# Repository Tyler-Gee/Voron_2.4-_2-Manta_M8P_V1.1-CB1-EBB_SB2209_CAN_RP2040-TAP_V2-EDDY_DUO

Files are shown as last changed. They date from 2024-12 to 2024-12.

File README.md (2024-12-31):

---
created: 2024-12-19T14:11
updated: 2024-12-22T21:22
---
# TODO
1. Create pdf Manual Chapters files for ever step. These files will follow relative path so they can be opened from within the REAMME.md file

# Formbot Voron 2.4 V2.4 R2 Pro+ Kit
- Store Link: https://www.aliexpress.com/item/1005003385349518.html?spm=a2g0o.order_list.order_list_main.59.318318027IHoca
- Github: Github: https://github.com/FORMBOT/Voron-2.4
- Review and Guide: https://www.youtube.com/watch?v=7x-eafpESLc

















# Components
## VoronDesigns:
github: https://github.com/VoronDesign/Voron-2

## TAP V2
Github:  https://github.com/VoronDesign/Voron-Tap

## Stealthburner
Github: https://github.com/VoronDesign/Voron-Stealthburner

## EBB SB2209 CAN (RP2040)
Github: https://github.com/bigtreetech/EBB

## MANTA M8P V1.0 & V1.1:
Github:  https://github.com/bigtreetech/Manta-M8P

## CB1
Github: https://github.com/bigtreetech/CB1

## Eddy Duo
- Store Link: https://www.aliexpress.com/item/1005006344907714.html?spm=a2g0o.order_list.order_list_main.23.318318027IHoca
- Github: https://github.com/bigtreetech/Eddy







## Belter
Store Link: https://www.aliexpress.com/item/1005007144698835.html?spm=a2g0o.order_list.order_list_main.17.318318027IHoca
Github: https://github.com/bigtreetech/Belter-belt-tension-Tool/tree/master

# Build Guide
## Part 0.0: Introduction
Manual: VORON2 2.4R2 Build Guide
- Pages: 0 - 11

## Part 1.0: Frame
Manual: VORON2 2.4R2 Build Guide
- Pages: 12 - 21

## Part 2.0: Z Drives
Manual: VORON2 2.4R2 Build Guide
- Pages: 22 - 51

## Part 3.0: Print Bed
Manual: VORON2 2.4R2 Build Guide
- Pages: 52 - 61

## Part 4.0: A/B Drives And Idlers
Manual: VORON2 2.4R2 Build Guide
- Pages: 62 - 81

## Part 5.0: Gantry
Manual: VORON2 2.4R2 Build Guide
- Pages: 82 - 107

## Part 6.0: Z Axis
Manual: VORON2 2.4R2 Build Guide
- Pages: 108 - 123

## Part 7.0: A/B Belts
Manual: VORON2 2.4R2 Build Guide
- Pages: 124 - 128
- Pages: 132 - 138

## Part 8.0: Tool head - Stealthburner
### Part 8.1: ClockWork2 Extruder
Manual: VORON STEALTHBURNER
- Pages: 0 - 40

### Part 8.2: Tool Cartridge
Manual: VORON STEALTHBURNER
- Pages: 41 - 43

### Part 8.3: Stealthburner
Manual: VORON STEALTHBURNER
- Pages: 44 - 57

### Part 8.4: Tap V2
Manual: VORON TAP

### Part 8.5: EBB SB2209 CAN (RP2040)
Manual: SB2240\2209 CAN V1.0
- Pages: 0 - 24

## Part 9.0: Check A/B Belt Run Inspection
Manual: VORON2 2.4R2 Build Guide
- Page: 142
Manual: Belter User Manual

## Part 10.0: Electronics
Manual: VORON2 2.4R2 Build Guide
- Pages: 148 - 173

## Part 11.0: Wiring
Manual: VORON2 2.4R2 Build Guide
- Pages: 0 - 11
Manual: Wiring Instructions for Voron 2.4 Pro
- Pages: 0 - 11
Manual: Instruction of V2.4 R2 Pro+
Manual: BIGTREETECH MANTA M8P V1.0&V1.1 User Manual
- Page: 11
Manual: EBB SB2209 CAN V1.0（RP2040）Build Guide_20240219
- Page: 7

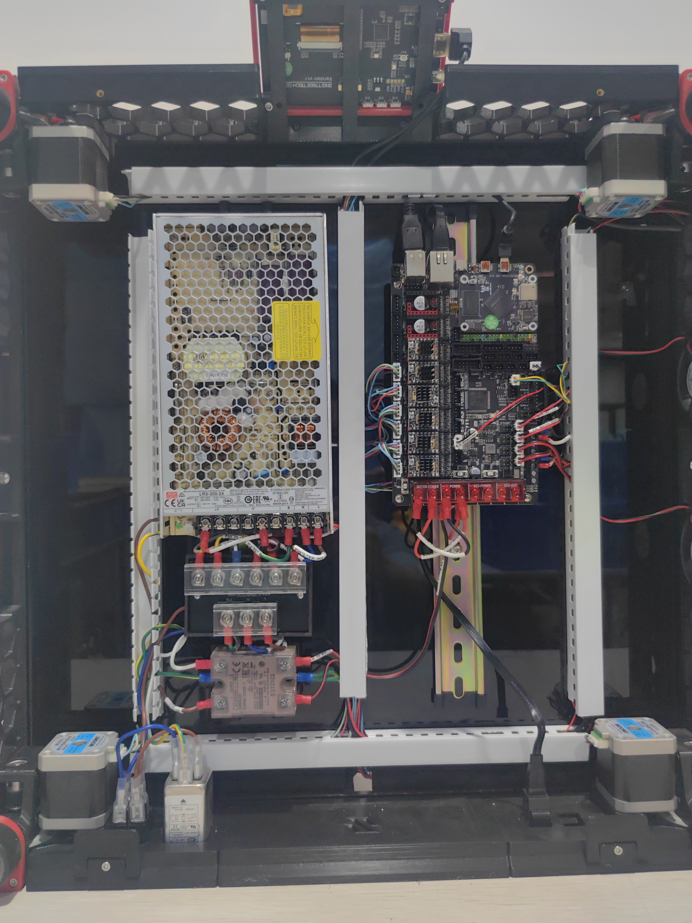
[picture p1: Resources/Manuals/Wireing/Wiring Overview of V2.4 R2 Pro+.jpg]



## Part 12.0: Manta M8P V1.1 + CB1
Manual: BIGTREETECH MANTA M8P V1.0&V1.1 User Manual
- Pages: 0 - 23

## Part 13.0: Skirts
Manual: VORON2 2.4R2 Build Guide
- Pages: 212 - 239

## Part 14.0: Panels
Manual: VORON2 2.4R2 Build Guide
- Pages: 240 - 259

## Part 16: Eddy Duo
Manual: BIGTRRETECH Eddy Series User Manual 20241210

# Flashing
## Overview
1. Put device into DFU Mode
2. Flash Katapult onto device
	- All devices of the same architecture flash the same way
	- Example: rp2040, stm, ect 
1. Put device into Katapult Mode
	- All devices of the same architecture flash the same way
	- Example: rp2040, stm, ect 
3. Flash klipper to device
4. Get UUID of canbus node

## OS Install
Manual: BIGTREETECH CB1 User Manual
- Pages: 13 - 18
Image: https://github.com/bigtreetech/CB1/releases

## MANTA M8P
Manual: BIGTREETECH MANTA M8P V1.0&V1.1 User Manual
- Pages: 33 - 39
Guides: 
1. @ [MAIN GUIDE]https://canbus.esoterical.online/mainboard_flashing.html
2. @ [MAIN RESOURCE]https://canbus.esoterical.online/mainboard_flashing/common_hardware/BigTreeTech%20Manta%20M8P%20v1.1/README.html
3. https://3dpandme.com/2022/10/02/tutorial-btt-manta-m8p-cb1-klipper-guide/
4. https://mpx.wiki/Firmware-Flash/flash-m8p-v1-ebb
5. https://gist.github.com/fredrikasberg/c14f08eb8617bf8981f77dbc01b00602
Github: https://github.com/bigtreetech/Manta-M8P

### DFU Mode
- Hold Boot0, Press Reset, Wait 5s, Release Boot0
### Flash Katapult
```bash
cd ~/katapult
make menuconfig
#	Micro-controller Architecture (STMicroelectronics STM32)  --->
#    Processor model (STM32G0B1)  --->
#    Build Katapult deployment application (8KiB bootloader)  --->
#    Clock Reference (8 MHz crystal)  --->
#    Communication interface (USB (on PA11/PA12))  --->
#    Application start offset (8KiB offset)  --->
#    USB ids  --->
#()  GPIO pins to set on bootloader entry
#[*] Support bootloader entry on rapid double click of reset button
#[ ] Enable bootloader entry on button (or gpio) state
#[*] Enable Status LED
#(PA13)  Status LED GPIO Pin

make clean
make

lsusb
## ID of STMicroelectronics STM DEvice in DFU Mode
## ID 0483:df11
sudo dfu-util -R -a 0 -s 0x08000000:leave -D ~/katapult/out/katapult.bin -d 0483:df11
```

### ### Enter Katapult Mode
- & double press reset button, red light indicates Katapult mode

### Flash Klipper
```bash
cd ~/klipper
make menuconfig
#[*] Enable extra low-level configuration options
#    Micro-controller Architecture (STMicroelectronics STM32)  --->
#    Processor model (STM32G0B1)  --->
#    Bootloader offset (8KiB bootloader)  --->
#    Clock Reference (8 MHz crystal)  --->
#    Communication interface (USB to CAN bus bridge (USB on PA11/PA12))  --->
#    CAN bus interface (CAN bus (on PD12/PD13))  --->
#    USB ids  --->
#(1000000) CAN bus speed
#()  GPIO pins to set at micro-controller startup
make clean
make
 
sudo service klipper stop
ls /dev/serial/by-id/
## usb-katapult_stm32g0b1xx_460041000A504B4633373520-if00
python3 ~/katapult/scripts/flashtool.py -f ~/klipper/out/klipper.bin -d /dev/serial/by-id/usb-katapult_your_board_id

ip -s -d link show can0
## Show bitrate is set to 1000000?

~/klippy-env/bin/python ~/klipper/scripts/canbus_query.py can0
## Found canbus_uuid=702c161f28a9, Application: Klipper
sudo service klipper start
```

## EBB SB2209C CAN RP2040 
Manual: EBB SB2209 CAN V1.0（RP2040）Build Guide_20240219
- Guides:
	1. @ [MAIN GUIDE]https://canbus.esoterical.online/toolhead_flashing
	2. @ [MAIN RESOURCE]https://canbus.esoterical.online/toolhead_flashing/common_hardware/BigTreeTech%20SB2209%20(RP2040)/README.html
	4. https://www.drklipper.de/doku.php?id=klipper_faq%3Aflash_guide%3Arp2040%3Aebb_sb2209_can
	5. https://www.youtube.com/watch?v=AYnoJCH7JJc&t=257s&ab_channel=Dr.Klipper
Github: https://github.com/bigtreetech/EBB/tree/master/EBB%20SB2209%20CAN%20(RP2040)

### Install Python
``` bash
sudo apt update
sudo apt upgrade
sudo apt install python3 python3-serial
```

### Enter DFU Mode
- Unplug CAN Cable
- Put jumper on 5v
- Connect USB power from the Manta M8P
- Hold Boot0, press Reset, Wait 5s, Release Boot0

### Flash Katapult
```bash
cd ~/katapult
make menuconfig
	Micro-controller Architecture (Raspberry Pi RP2040/RP235x) ->
	Processor model (rp2040)  --->
	Flash chip (W25Q080 with CLKDIV 2)  --->
	Build Katapult deployment application (16KiB bootloader)  ->
    Communication Interface (CAN bus)  --->
(4) CAN RX gpio number (NEW)
(5) CAN TX gpio number (NEW)
(250000) CAN bus speed
()  GPIO pins to set on bootloader entry
[*] Support bootloader entry on rapid double click of reset button
[ ] Enable bootloader entry on button (or gpio) state
[*] Enable Status LED
(gpio26) Status LED GPIO Pin
make clean
make 

lsusb
## ID of rp2040 in boot mode
make flash FLASH_DEVICE=2e8a:0003
```

### !IMPORTANT! Remove Jumper BEFORE Continuing
- ! REMOVE Jumper or board will be fried

### Connect to 24 V
- ! DOUBLE CHECK, Jumper has been Removed
- Plug in Can Cable

### Enter Katapult Mode
- & double press reset button, red light indicates Katapult mode

### Flash Klipper
```bash
cd ~/klilpper
make menuconfig
	[*] Enable extra low-level configuration options
    Micro-controller Architecture (Raspberry Pi RP2040/RP235x)  --->
    Processor model (rp2040)  --->
    Bootloader offset (16KiB bootloader)  --->
    Communication Interface (CAN bus)  --->
(4) CAN RX gpio number (NEW)
(5) CAN TX gpio number (NEW)
(1000000) CAN bus speed
(gpio26)  GPIO pins to set at micro-controller startup
make clean
make

sudo service klipper stop
# Grab UUID from Katapult Node.
python3 ~/katapult/scripts/flashtool.py -i can0 -q
python3 ~/katapult/scripts/flashtool.py -i can0 -u <~youruuid~~> -f ~/klipper/out/klipper.bin
##Katapult Node should now be Klipper
~/klippy-env/bin/python ~/klipper/scripts/canbus_query.py can0
sudo service klipper start
## Detected UUID: 5a2de1007cc7, Application: Klipper
```

## Eddy
Manual: EBB SB2209 CAN V1.0（RP2040）Build Guide_20240219
- Guides:
Github: https://github.com/bigtreetech/Eddy

### Enter DFU Mode
- & Ensure Eddy Duo is Set to USB Mode
- Plug USB Cable into Manta M8P
- Hold down Boot Button, Plug in Eddy

### Flash Katapult
```bash
cd ~/katapult
make menuconfig
Micro-controller Architecture (Raspberry Pi RP2040/RP235x)  --->
    Processor model (rp2040)  --->
    Flash chip (W25Q080 with CLKDIV 2)  --->
    Build Katapult deployment application (16KiB bootloader)  --->
    Communication Interface (CAN bus)  --->
(4) CAN RX gpio number
(5) CAN TX gpio number
(1000000) CAN bus speed
()  GPIO pins to set on bootloader entry
[*] Support bootloader entry on rapid double click of reset button
[ ] Enable bootloader entry on button (or gpio) state
[*] Enable Status LED
(gpio26) Status LED GPIO Pin
make clean
make

lsusb
## Bus 002 Device 005: ID 2e8a:0003 Raspberry Pi RP2 Boot
make flash FLASH_DEVICE=2e8a:0003
```

### Toggle CAN Mode
- & On Back of Eddy, Switch USB to CAN
- Plug Eddy into Tool Head Harness
- & NO DFU Mode Needed

### Flash Klipper
```bash
sudo service klipper stop
cd ~/klipper
make menuconfig
[*] Enable extra low-level configuration options
    Micro-controller Architecture (Raspberry Pi RP2040/RP235x)  --->
    Processor model (rp2040)  --->
    Bootloader offset (16KiB bootloader)  --->
    Communication Interface (CAN bus)  --->
(4) CAN RX gpio number
(5) CAN TX gpio number
(1000000) CAN bus speed
(gpio26) GPIO pins to set at micro-controller startup
make clean
make

sudo service klipper stop
# Grab UUID from Katapult Node.
## Detected UUID: 21c888bd553a, Application: Katapult
python3 ~/katapult/scripts/flashtool.py -i can0 -q
python3 ~/katapult/scripts/flashtool.py -i can0 -u <~youruuid~~> -f ~/klipper/out/klipper.bin
##Katapult Node should now be Klipper
~/klippy-env/bin/python ~/klipper/scripts/canbus_query.py can0
sudo service klipper start
## Detected UUID: 5a2de1007cc7, Application: Klipper

# Manta M8P
##Detected UUID: 702c161f28a9, Application: Klipper
# Eddy
##Detected UUID: 21c888bd553a, Application: Klipper
# Toolhead
##Detected UUID: 5a2de1007cc7, Application: Klipper
```

## KAIUH
Github: https://github.com/dw-0/kiauh
```bash
cd ~/kiauh
./kiauh.sh
## Install Fluid and Fluid Client-Config
## Update everything
```

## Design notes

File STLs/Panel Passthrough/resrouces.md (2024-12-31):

LINK: https://www.printables.com/model/418591-bowden-panel-passthrough

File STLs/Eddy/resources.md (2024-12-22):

---
created: 2024-12-20T08:23
updated: 2024-12-20T08:23
---
Link: https://www.printables.com/model/952155-btt-eddy-clip-for-stealthburner-tz-v2-tz-v6-20-ext
TLDR:
    Measured from the model, the offsets of the probe for klipper are x_offset: -48.014, y_offset: -6.05

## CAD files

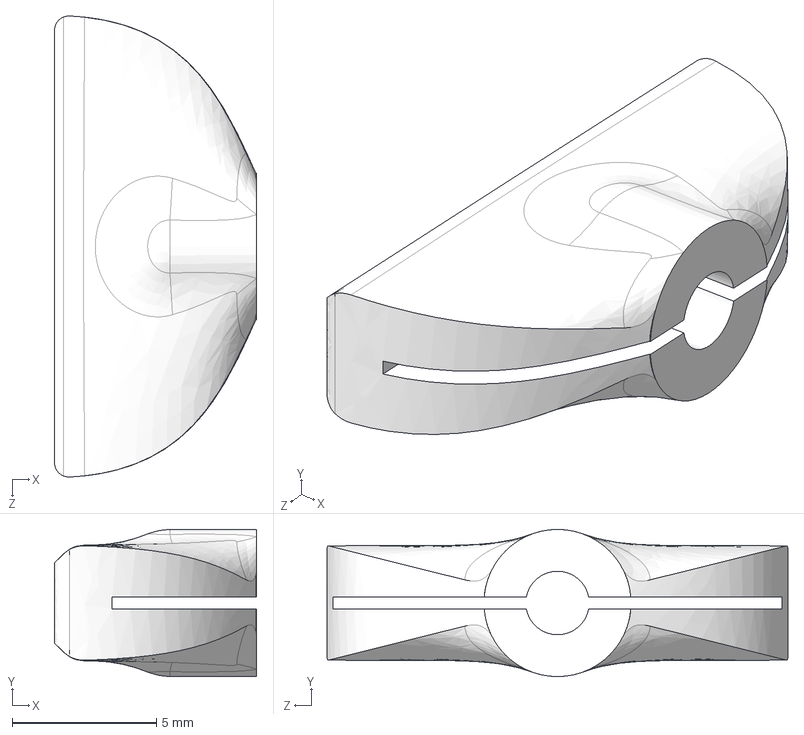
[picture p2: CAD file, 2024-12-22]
STLs/Belter/ProbeTip.STEP
7.00 x 5.10 x 16.0 mm

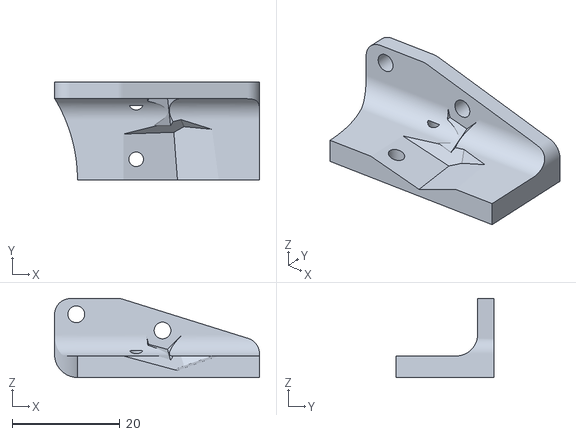
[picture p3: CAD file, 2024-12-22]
STLs/Eddy/EddyClip.stl
38.0 x 18.1 x 14.7

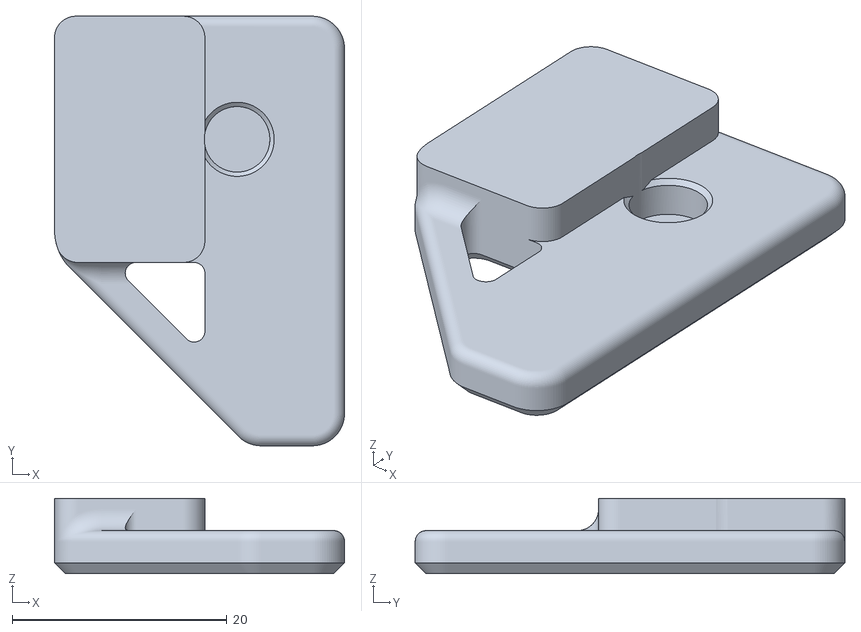
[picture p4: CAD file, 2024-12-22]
STLs/Panel_Mounting/Front_Doors/handle_a_x2.stl
27.0 x 40.0 x 7.00

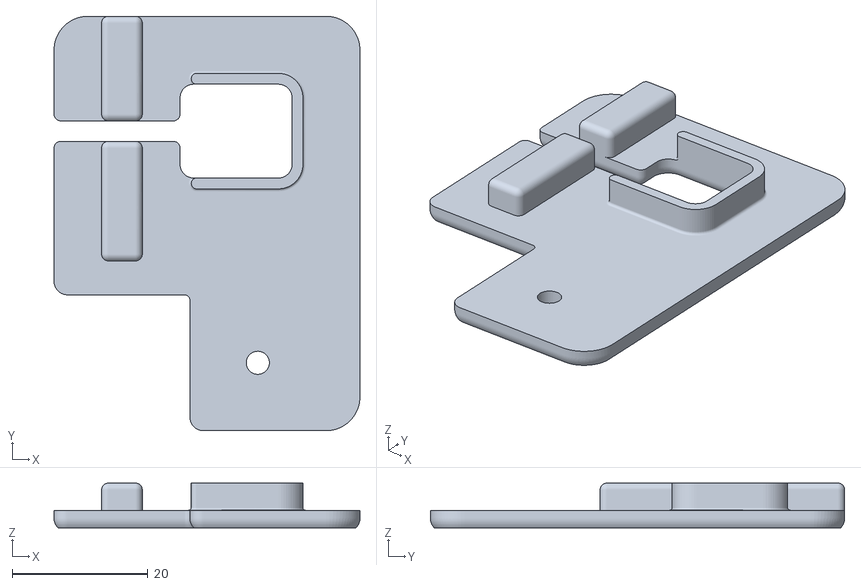
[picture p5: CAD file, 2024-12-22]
STLs/Panel_Mounting/z_belt_cover_b_x2.stl
45.0 x 61.0 x 6.60

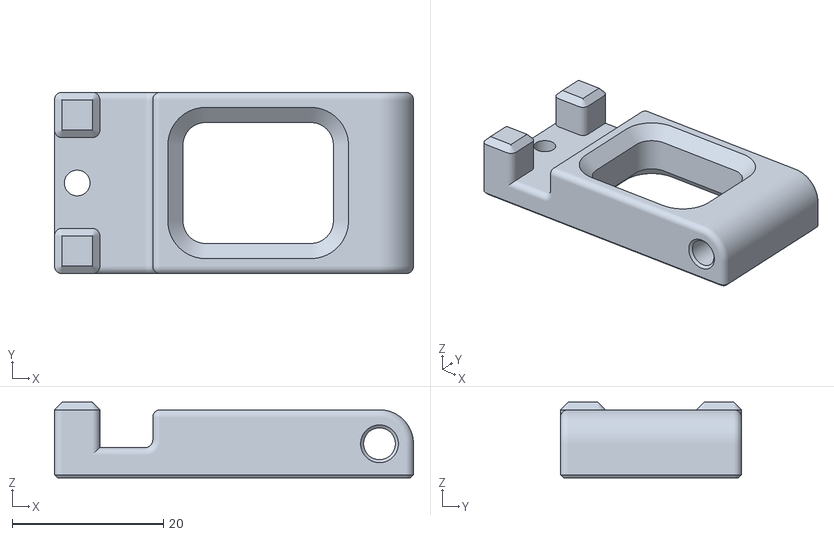
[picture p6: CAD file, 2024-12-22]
STLs/Spool_Management/bowden_retainer.stl
47.5 x 24.0 x 10.00

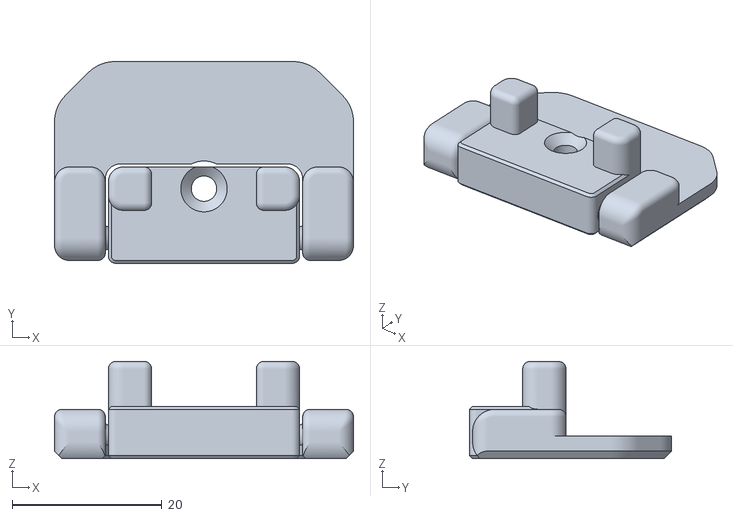
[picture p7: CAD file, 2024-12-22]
STLs/Panel_Mounting/Front_Doors/door_hinge_x6.stl
40.0 x 27.0 x 13.0

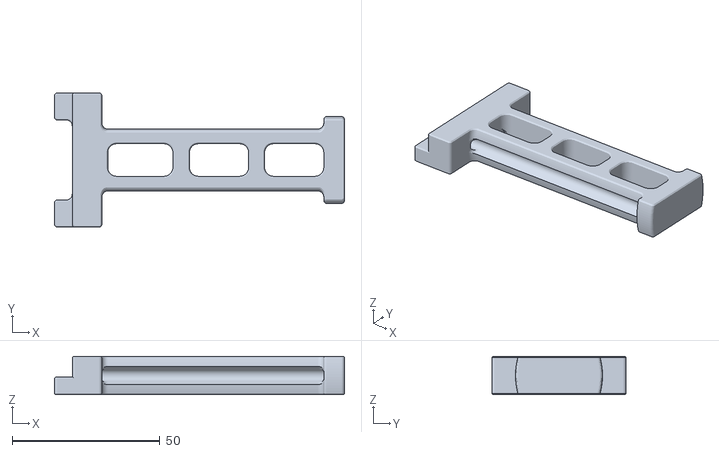
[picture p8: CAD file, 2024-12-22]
STLs/Spool_Management/spool_holder.stl
98.0 x 45.4 x 13.0

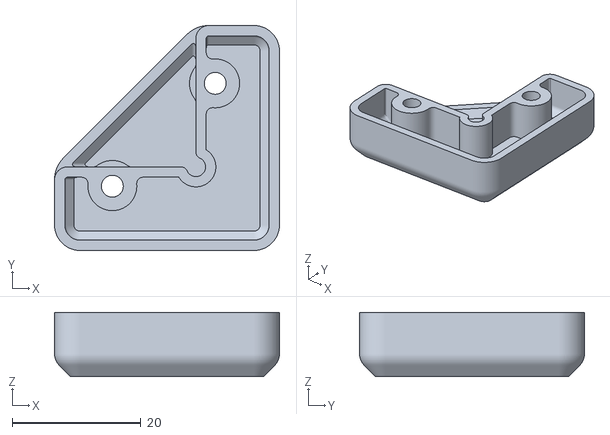
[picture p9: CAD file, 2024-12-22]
STLs/Panel_Mounting/corner_panel_clip_6mm_x8.stl
35.0 x 35.0 x 10.00

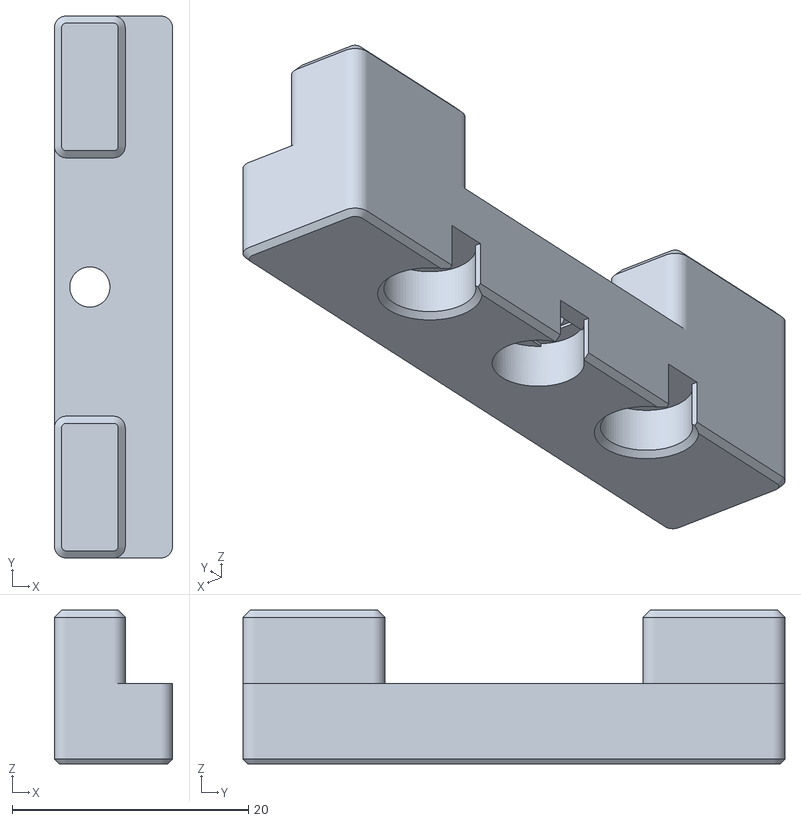
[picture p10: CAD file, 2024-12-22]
STLs/Panel_Mounting/Front_Doors/latch_x2.stl
10.0 x 45.9 x 13.0

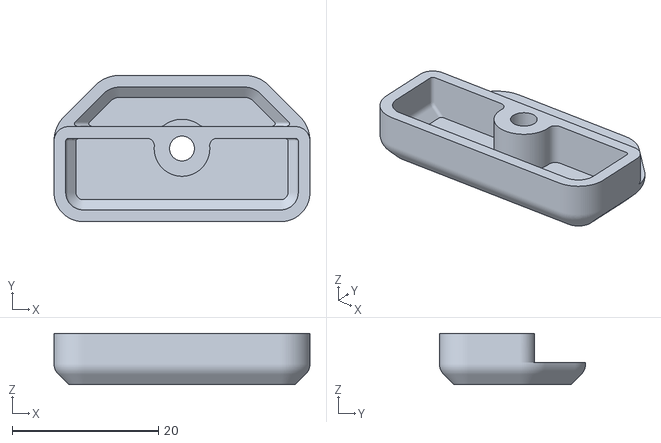
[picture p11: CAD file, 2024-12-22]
STLs/Panel_Mounting/midspan_panel_clip_4mm_x7.stl
35.0 x 20.0 x 7.00

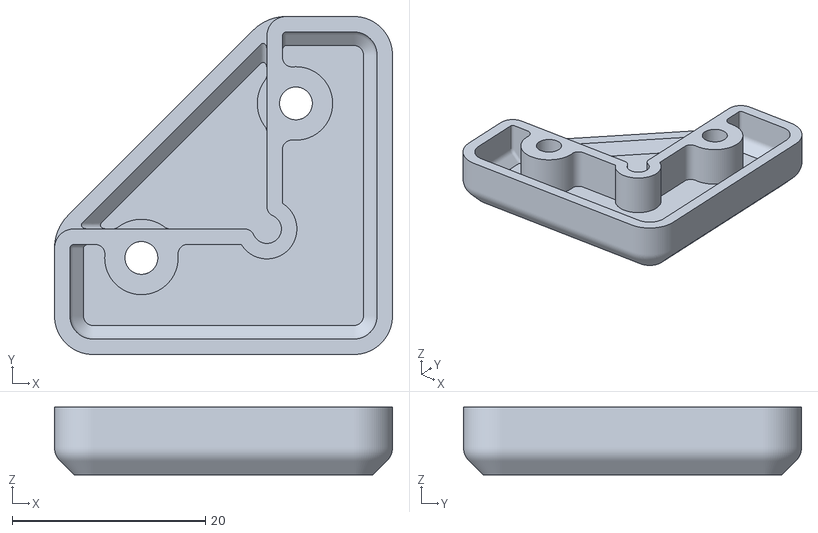
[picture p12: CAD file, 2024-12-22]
STLs/Panel_Mounting/corner_panel_clip_4mm_x8.stl
35.0 x 35.0 x 7.00

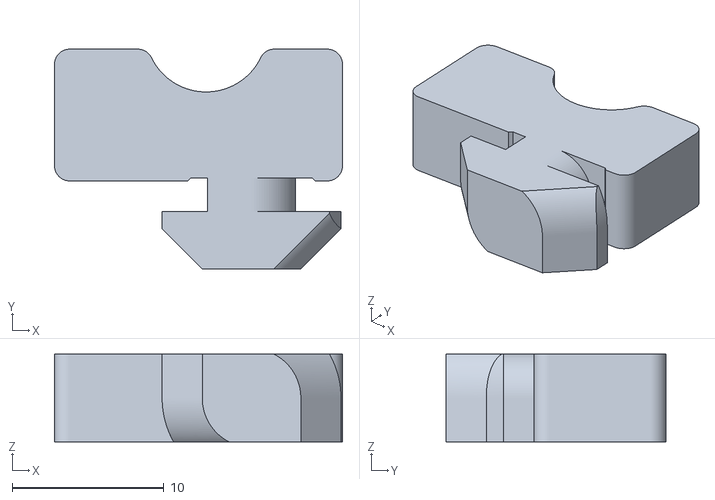
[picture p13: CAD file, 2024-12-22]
STLs/Panel_Mounting/deck_support_4mm_x8.stl
19.0 x 14.5 x 5.80

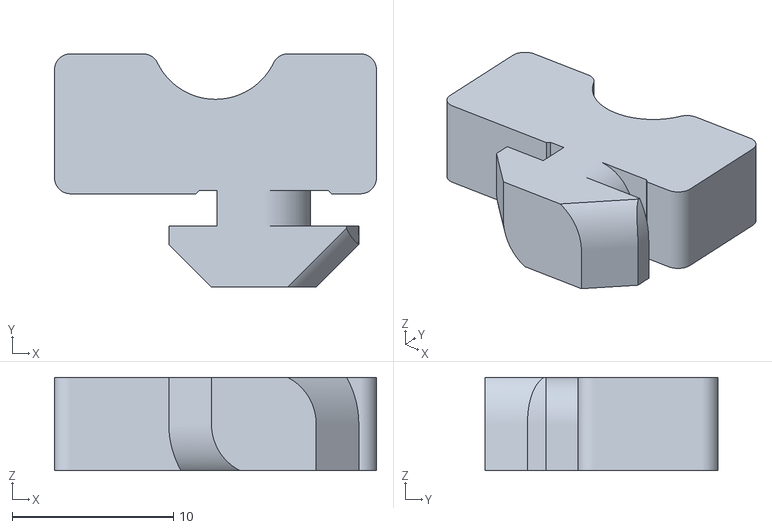
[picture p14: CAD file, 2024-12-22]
STLs/Panel_Mounting/deck_support_3mm_x8.stl
20.0 x 14.5 x 5.80

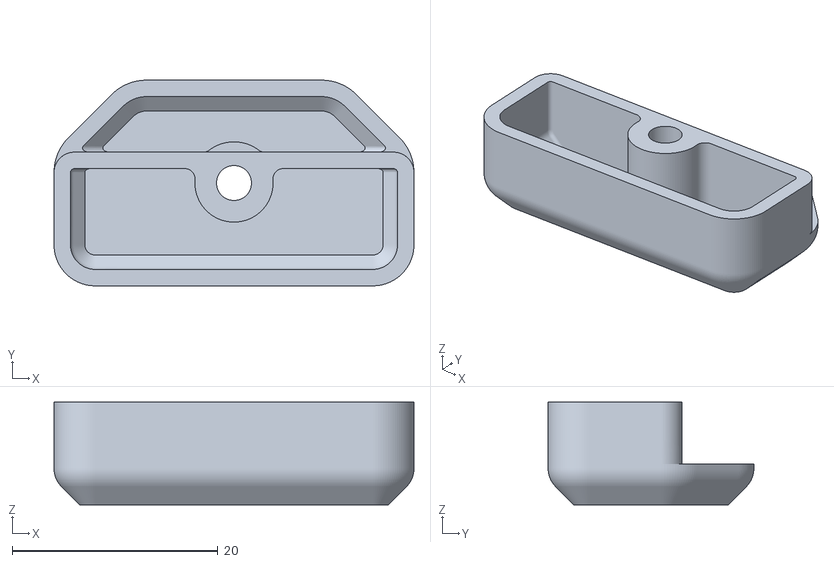
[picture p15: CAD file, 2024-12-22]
STLs/Panel_Mounting/midspan_panel_clip_6mm_x8.stl
35.0 x 20.0 x 10.00

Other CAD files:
STLs/Eddy/BTT Eddy Clip v3.step
STLs/Panel_Mounting/z_belt_cover_a_x2.stl
STLs/Panel_Mounting/Front_Doors/handle_b_x2.stl
STLs/Panel_Mounting/bottom_panel_clip_x4.stl
STLs/Panel_Mounting/bottom_panel_hinge_x2.stl

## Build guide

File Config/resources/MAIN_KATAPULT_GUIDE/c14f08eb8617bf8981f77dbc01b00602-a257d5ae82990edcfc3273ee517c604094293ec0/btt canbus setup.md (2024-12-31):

# BTT Manta M8P v1.1 + BTT EBB 2209 Canbus setup

Since documentation has been somewhat lacking... here is a quick write-up to get started!

Sources:

* https://github.com/Esoterical/voron_canbus/tree/main/toolhead_flashing/common_hardware/BigTreeTech%20SB2209%20and%20SB2240
* https://github.com/bigtreetech/EBB/blob/master/EBB%20SB2240_2209%20CAN/sample-bigtreetech-ebb-sb-canbus-v1.0.cfg

Boards:
* [Manta M8P](https://github.com/bigtreetech/Manta-M8P)
* [EBB2209](https://github.com/bigtreetech/EBB/tree/master/EBB%20SB2240_2209%20CAN)

**NOTE** This guide assumes that you are running Mainsail (Raspbian Buster). While the firmware compilation/flashing is more or less the same on all systems there will probably be differences in configuring the canbus interface if you are running a newer version of Raspbian (Bookworm or later). 

Systemd configuration by [@yzheka](https://github.com/yzheka) in the [comments](https://gist.github.com/fredrikasberg/c14f08eb8617bf8981f77dbc01b00602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).

## Manta M8P

**NOTE** Do not forget the `120R` jumper just above the canbus connector!

[Board overview](https://github.com/bigtreetech/Manta-M8P/blob/master/Hardware/BIGTREETECH%20MANTA%20M8P%20V1.1%20PinOut.png)

### Katapult (previously CanBoot)

As [julianschweizer](https://gist.github.com/fredrikasberg/c14f08eb8617bf8981f77dbc01b00602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) pointed out, the **CanBoot** project has been renamed **Katapult**

First, ssh into your system and from the home directory pull the latest version of katapult

```git clone https://github.com/Arksine/katapult.git```

Enter directory and compile Katapult

```
cd ~/katapult
make menuconfig
```

Use the following config

```
Micro-controller Architecture (STMicroelectronics STM32)  --->
Processor model (STM32G0B1)  --->
Build CanBoot deployment application (Do not build)  --->
Clock Reference (8 MHz crystal)  --->
Communication interface (CAN bus (on PD12/PD13))  --->
Application start offset (8KiB offset)  --->
(250000) CAN bus speed
() GPIO pins to set on bootloader entry
[*] Support bootloader entry on rapid double click of reset button
[ ] Enable bootloader entry on button (or gpio) state
[ ] Enable Status LED
```

Now build Katapult

```
make clean
make
```

### Klipper

Enter klipper directory and compile klipper

```
cd ~/klipper
make menuconfig
```

Use the following configuration

```
[*] Enable extra low-level configuration options
Micro-controller Architecture (STMicroelectronics STM32) --->
Processor model (STM32G0B1) --->
Bootloader offset (8KiB bootloader) --->
Clock Reference (8 MHz crystal) --->
Communication interface (USB to CAN bus bridge (USB on PA11/PA12)) --->
CAN bus interface (CAN bus (on PD12/PD13)) --->
USB ids --->
(250000) CAN bus speed
() GPIO pins to set at micro-controller startup
```

Now build klipper

```
make clean
make
```

### Flashing Katapult and Klipper

First flash your Manta M8P by entering DFU mode

1. Hold down `Boot0` AND `Reset`
2. Release Reset and then `Boot0`

Make sure that your board is in DFU mode by running

```lsusb```

This should show you the Manta M8P as `Bus 001 Device 008: ID 0483:df11 STMicroelectronics STM Device in DFU Mode`.

When you have validated that the Manta M8P is ready, flash Katapult.

```sudo dfu-util -a 0 -D ~/katapult/out/katapult.bin --dfuse-address 0x08000000:force:leave -d 0483:df11```

Then reset the board by pressing `Reset` and then put the board in DFU mode once again to flash Klipper.

```sudo dfu-util -a 0 -d 0483:df11 --dfuse-address 0x08002000 -D ~/klipper/out/klipper.bin```

Now the board should be running Katapult with Klipper. Verify by pressing `Reset` once again and then run `lsusb`.
The board should be identified by `Bus 001 Device 011: ID 1d50:606f OpenMoko, Inc. Geschwister Schneider CAN adapter`.

### Enable Canbus on the Raspberry Pi

To enable the canbus on the raspberry pi you need to create the interface file

```
sudo nano /etc/network/interfaces.d/can0
```

Paste the following content
```
allow-hotplug can0
iface can0 can static
 bitrate 250000
 up ifconfig $IFACE txqueuelen 1024
```

To bring the canbus interface `can0` up simply run `sudo ifup can0`. If everything worked you should now be able to query your Manta board using `python3 ~/katapult/scripts/flash_can.py -q`.
This command will present you with the UUID of the Manta board which you need to reference in your `printer.cfg`.

```
[mcu]
canbus_uuid: <your uuid goes here>
canbus_interface: can0
```

## BTT EBB2209

The procedure is more or less the same for the EBB2209 board.

**NOTE** I don't know with 100% certainty that the heater won't turn on when the board is in DFU mode so keep the heater cartridge disconnected just to be safe!

**NOTE** Do not forget the `120R` jumper on the bottom of the board (beside BL-Touch connector)!

### Katapult

Just enter the `katapult` folder from the last step and re-run `menuconfig`.

```
cd ~/katapult
make menuconfig
```

Use the followin config

```
[*] Enable extra low-level conﬁguration options
Micro-controller Architecture (STMicroelectronics STM32) --->
Processor model (STM32G0B1) --->
Bootloader oﬀset (8KiB bootloader) --->
Clock Reference (8 MHz crystal) --->
Communication interface (CAN bus (on PB0/PB1)) --->
(250000) CAN bus speed
```

Now compile Katapult

```
make clean
make
```

### Klipper

Enter klipper directory and compile klipper

```
cd ~/klipper
make menuconfig
```

Use the following config

```
[*] Enable extra low-level conﬁguration options
Micro-controller Architecture (STMicroelectronics STM32) --->
Processor model (STM32G0B1) --->
Bootloader oﬀset (8KiB bootloader) --->
Clock Reference (8 MHz crystal) --->
Communication interface (CAN bus (on PB0/PB1)) --->
(250000) CAN bus speed
```

### Flashing Katapult and Klipper

[Board overview](https://github.com/bigtreetech/EBB/blob/master/EBB%20SB2240_2209%20CAN/SB2209/Hardware/BIGTREETECHEBB%20SB2209%20CAN%20V1.0_IO.pdf)

First flash your EBB2209 by entering DFU mode

1. Hold down `Boot` AND `Rst`
2. Release Reset and then `Boot`

Make sure that your board is in DFU mode by running

```lsusb```

This should show you the EBB22009 as `Bus 001 Device 008: ID 0483:df11 STMicroelectronics STM Device in DFU Mode`.

When you have validated that the board is ready, flash Katapult.

```sudo dfu-util -a 0 -D ~/katapult/out/katapult.bin --dfuse-address 0x08000000:force:leave -d 0483:df11```

Then reset the board by pressing `Rst` and then put the board in DFU mode once again to flash Klipper.

```sudo dfu-util -a 0 -d 0483:df11 --dfuse-address 0x08002000 -D ~/klipper/out/klipper.bin```

Now the board should be running Katapult with Klipper. Verify by pressing `Reset` once again and then run `lsusb`.
The board should be identified by `Bus 001 Device 011: ID 1d50:606f OpenMoko, Inc. Geschwister Schneider CAN adapter`.

Since you already have a canbus network up and running, simply run `python3 ~/katapult/scripts/flash_can.py -q` to get the UUID for the EBB2209 board.

Using the UUID from that command you should reference the board the same way you did your Manta board but this time with a identifier.

```
[mcu EBBCan]
canbus_uuid: <your uuid goes here>
canbus_interface: can0
```

Now you need to update your printer configuration to use the appropriate pins and if you named your mcu `EBBCan` you can more or less copy the [example configuration](https://github.com/bigtreetech/EBB/blob/master/EBB%20SB2240_2209%20CAN/sample-bigtreetech-ebb-sb-canbus-v1.0.cfg)!

Happy printing!

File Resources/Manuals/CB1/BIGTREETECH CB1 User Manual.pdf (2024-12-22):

Shenzhen Big Tree Technology Co., Ltd.

## BIGTREETECH

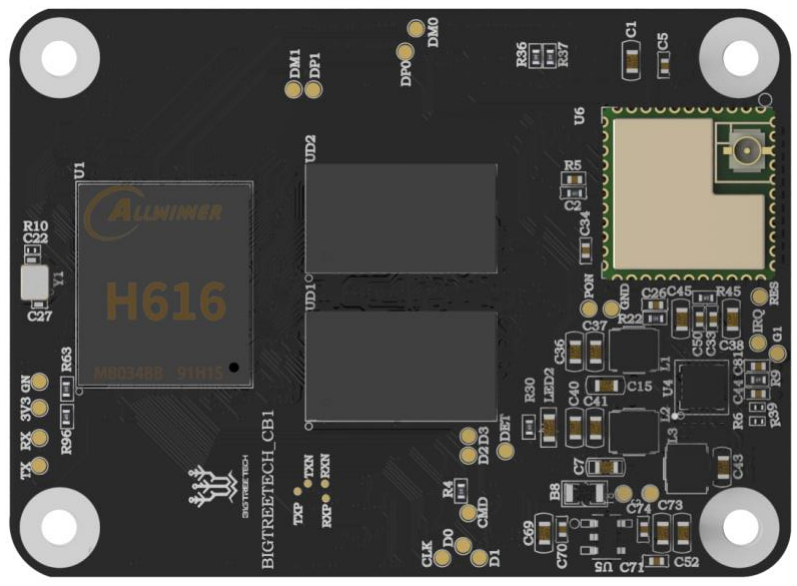
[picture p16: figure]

1 / 22

# BIGTREETECH

CB1

# User Manual

## BIGTREETECH

2 / 22

# CONTENTS

## BIGTREETECH

3 / 22

# Revision History

Version | Revisions | Date
01.00 | Original | 2022/09/20

## BIGTREETECH

4 / 22

# 1. Product Profile

### The BIGTREETECH CB1 is launched to provide a great solution to the insane shortage of Raspberry Pi CM4. It outputs signals to the motherboard via the fast and

convenient two 100 pins micro BTB connection header, including 100M Ethernet, HDMI, etc. Also, onboard 2.4G WiFi.

## 1.1 Feature Highlights

### 1. CPU: ALLWINNER H616, Quad-core Cortex-A53 @1.5GHz

### 2. GPU: Mali G31 MP2, Support OpenGL3.2

### 3. RAM: 512MB/1GB DDR3L SDRAM

### 4. Display: Compatible with HDMI2.0A Interface, Support 4K Displays

### 5. Compatible with USB2.0 Interface

### 6. Support 100M Ethernet + 100M WiFi

7. Having the same BTB header as the Raspberry Pi CM4.

## 1.2 Specifications

### 1. Product Size: 40mm x 55mm

### 2. Mounting Size: 33mm x 48mm

### 3. Input Voltage: 5V±5%/2A

### 4. Output Voltage: 3.3V±2%/100mA

### 5. Output Voltage: 1.8V±2%/100mA

### 6. WiFi: 2.4G/802.11 b/g/n

## BIGTREETECH

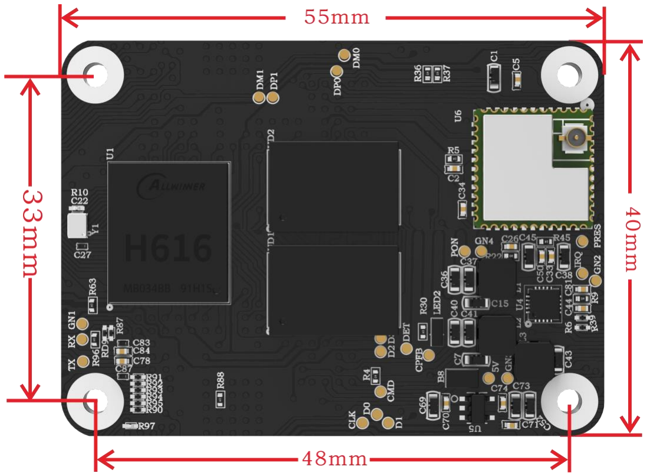
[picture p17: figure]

5 / 22

## 1.3 Dimensions

# 2 Peripheral Port

## 2.1 Pin

PIN | Connector | Signal | Description
1 | A connector_01 | GND
2 | A connector_02 | GND
3 | A connector_03 | NC
4 | A connector_04 | EPHY-TXP | Ethernet TX Positive
5 | A connector_05 | NC
6 | A connector_06 | EPHY-TXN | Ethernet TX Negative
7 | A connector_07 | GND
8 | A connector_08 | GND
9 | A connector_09 | NC
10 | A connector_10 | EPHY-RXP | Ethernet RX Positive
11 | A connector_11 | NC
12 | A connector_12 | EPHY-RXN | Ethernet RX Negative
13 | A connector_13 | GND

## BIGTREETECH

6 / 22

14 | A connector_14 | GND
15 | A connector_15 | LINK_LED | Ethernet LED
16 | A connector_16 | NC
17 | A connector_17 | SPD_LED | Ethernet LED
18 | A connector_18 | NC
19 | A connector_19 | NC
20 | A connector_20 | NC
21 | A connector_21 | SYS-LED | System work light
22 | A connector_22 | GND
23 | A connector_23 | GND
24 | A connector_24 | PC15 | 3.3V IO(CB1 V2.1 is 1.8v )
25 | A connector_25 | PC8 | 3.3V IO(CB1 V2.1 is 1.8v )
26 | A connector_26 | PC6 | 3.3V IO(CB1 V2.1 is 1.8v )
27 | A connector_27 | PH10 | 3.3V IO
28 | A connector_28 | NC
29 | A connector_29 | NC
30 | A connector_30 | PG6 | 3.3V IO
31 | A connector_31 | PG9 | 3.3V IO
32 | A connector_32 | GND
33 | A connector_33 | GND
34 | A connector_34 | NC
35 | A connector_35 | PG7 | 3.3V IO
36 | A connector_36 | NC
37 | A connector_37 | PG8 | 3.3V IO
38 | A connector_38 | PH6 | 3.3V IO
39 | A connector_39 | NC | 3.3V IO
40 | A connector_40 | PH8 | 3.3V IO
41 | A connector_41 | NC
42 | A connector_42 | GND
43 | A connector_43 | GND
44 | A connector_44 | PH7 | 3.3V IO
45 | A connector_45 | PC9 | 3.3V IO(CB1 V2.1 is 1.8v )
46 | A connector_46 | PC10 | 3.3V IO(CB1 V2.1 is 1.8v )
47 | A connector_47 | PC11 | 3.3V IO(CB1 V2.1 is 1.8v )
48 | A connector_48 | PC12 | 3.3V IO(CB1 V2.1 is 1.8v )
49 | A connector_49 | PC13 | 3.3V IO(CB1 V2.1 is 1.8v )
50 | A connector_50 | PC14 | 3.3V IO(CB1 V2.1 is 1.8v )
51 | A connector_51 | SoC_RX | DEBUG UART
52 | A connector_52 | GND
53 | A connector_53 | GND
54 | A connector_54 | PC7 | 3.3V IO(CB1 V2.1 is 1.8v )
55 | A connector_55 | SoC_TX | DEBUG UART
56 | A connector_56 | NC
57 | A connector_57 | SDC0-CLK | SDCARD Clock signal

## BIGTREETECH

7 / 22

58 | A connector_58 | NC
59 | A connector_59 | GND
60 | A connector_60 | GND
61 | A connector_61 | SDC0-D3 | SDCARD Data3 signal
62 | A connector_62 | SDC0-CMD | SDCARD CMD signal
63 | A connector_63 | SDC0-D0 | SDCARD Data0 signal
64 | A connector_64 | PG11 | 3.3V IO
65 | A connector_65 | GND
66 | A connector_66 | GND
67 | A connector_67 | SDC0-D1 | SDCARD Data1 signal
68 | A connector_68 | PG12 | 3.3V IO
69 | A connector_69 | SDC0-D2 | SDCARD Data2 signal
70 | A connector_70 | PG13 | 3.3V IO
71 | A connector_71 | GND
72 | A connector_72 | PG14 | 3.3V IO
73 | A connector_73 | PG16 | 3.3V IO
74 | A connector_74 | GND
75 | A connector_75 | NC
76 | A connector_76 | SDC0-DET | SDCARD detect
77 | A connector_77 | VCC_5V | 5V IN /2A
78 | A connector_78 | NC
79 | A connector_79 | VCC_5V | 5V IN /2A
80 | A connector_80 | NC
81 | A connector_81 | VCC_5V | 5V IN /2A
82 | A connector_82 | NC
83 | A connector_83 | VCC_5V | 5V IN /2A
84 | A connector_84 | 3V3 | 3.3V out /200mA
85 | A connector_85 | VCC_5V | 5V IN /2A
86 | A connector_86 | 3V3 | 3.3V out /200mA
87 | A connector_87 | VCC_5V | 5V IN /2A
88 | A connector_88 | 1V8 | 1.8V out /100mA
89 | A connector_89 | NC
90 | A connector_90 | 1V8 | 1.8V out /100mA
91 | A connector_91 | NC
92 | A connector_92 | PWRON | Power switch (useless)
93 | A connector_93 | FEL | (useless)
94 | A connector_94 | NC
95 | A connector_95 | NC
96 | A connector_96 | NC
97 | A connector_97 | NC
98 | A connector_98 | GND
99 | A connector_99 | RECOVERY | Program download (useless)
100 | A connector_100 | AP-RESET | power reset (useless)
101 | B connector_1 | NC

## BIGTREETECH

8 / 22

102 | B connector_2 | NC
103 | B connector_3 | USB1-DM | HOST USB1
104 | B connector_4 | LINEOUTL
105 | B connector_5 | USB1-DP | HOST USB1
106 | B connector_6 | LINEOUTR
107 | B connector_7 | GND
108 | B connector_8 | GND
109 | B connector_9 | NC
110 | B connector_10 | NC
111 | B connector_11 | TV_OUT | CVBS OUT
112 | B connector_12 | NC
113 | B connector_13 | GND
114 | B connector_14 | GND
115 | B connector_15 | NC
116 | B connector_16 | NC
117 | B connector_17 | NC
118 | B connector_18 | NC
119 | B connector_19 | GND
120 | B connector_20 | GND
121 | B connector_21 | NC
122 | B connector_22 | NC
123 | B connector_23 | NC
124 | B connector_24 | NC
125 | B connector_25 | GND
126 | B connector_26 | GND
127 | B connector_27 | NC
128 | B connector_28 | USB3-DM | HOST USB3
129 | B connector_29 | NC
130 | B connector_30 | USB3-DP | HOST USB3
131 | B connector_31 | GND
132 | B connector_32 | GND
133 | B connector_33 | NC
134 | B connector_34 | USB2-DM | HOST USB2
135 | B connector_35 | NC
136 | B connector_36 | USB2-DP | HOST USB2
137 | B connector_37 | GND
138 | B connector_38 | GND
139 | B connector_39 | NC
140 | B connector_40 | USB0-DM | OTG USB
141 | B connector_41 | NC
142 | B connector_42 | USB0-DP | OTG USB
143 | B connector_43 | NC
144 | B connector_44 | GND
145 | B connector_45 | NC

## BIGTREETECH

9 / 22

146 | B connector_46 | NC
147 | B connector_47 | NC
148 | B connector_48 | NC
149 | B connector_49 | NC
150 | B connector_50 | GND
151 | B connector_51 | HCEC | HDMI CEC
152 | B connector_52 | NC
153 | B connector_53 | HHPD | HDMI Hotplug
154 | B connector_54 | NC
155 | B connector_55 | GND
156 | B connector_56 | GND
157 | B connector_57 | NC
158 | B connector_58 | NC
159 | B connector_59 | NC
160 | B connector_60 | NC
161 | B connector_61 | GND
162 | B connector_62 | GND
163 | B connector_63 | NC
164 | B connector_64 | NC
165 | B connector_65 | NC
166 | B connector_66 | NC
167 | B connector_67 | GND
168 | B connector_68 | GND
169 | B connector_69 | NC
170 | B connector_70 | HTX2P | HDMI TX2 Positive.
171 | B connector_71 | NC
172 | B connector_72 | HTX2N | HDMI TX2 Negative.
173 | B connector_73 | GND
174 | B connector_74 | GND
175 | B connector_75 | NC
176 | B connector_76 | HTX1P | HDMI TX1 Positive.
177 | B connector_77 | NC
178 | B connector_78 | HTX1N | HDMI TX1 Negative.
179 | B connector_79 | GND
180 | B connector_80 | GND
181 | B connector_81 | NC
182 | B connector_82 | HTX0P | HDMI TX0 Positive.
183 | B connector_83 | NC
184 | B connector_84 | HTX0N | HDMI TX0 Negative.
185 | B connector_85 | GND
186 | B connector_86 | GND
187 | B connector_87 | NC
188 | B connector_88 | HTXCP | HDMI CLK Positive.
189 | B connector_89 | NC

## BIGTREETECH

10 / 22

190 | B connector_90 | HTXCN | HDMI CLK Negative.
191 | B connector_91 | GND
192 | B connector_92 | GND
193 | B connector_93 | NC
194 | B connector_94 | NC
195 | B connector_95 | NC
196 | B connector_96 | NC
197 | B connector_97 | GND
198 | B connector_98 | GND
199 | B connector_99 | HSDA | HDMI I2C
200 | B connector_100 | HSCL | HDMI I2C

## BIGTREETECH

# 3. Interface Introduction

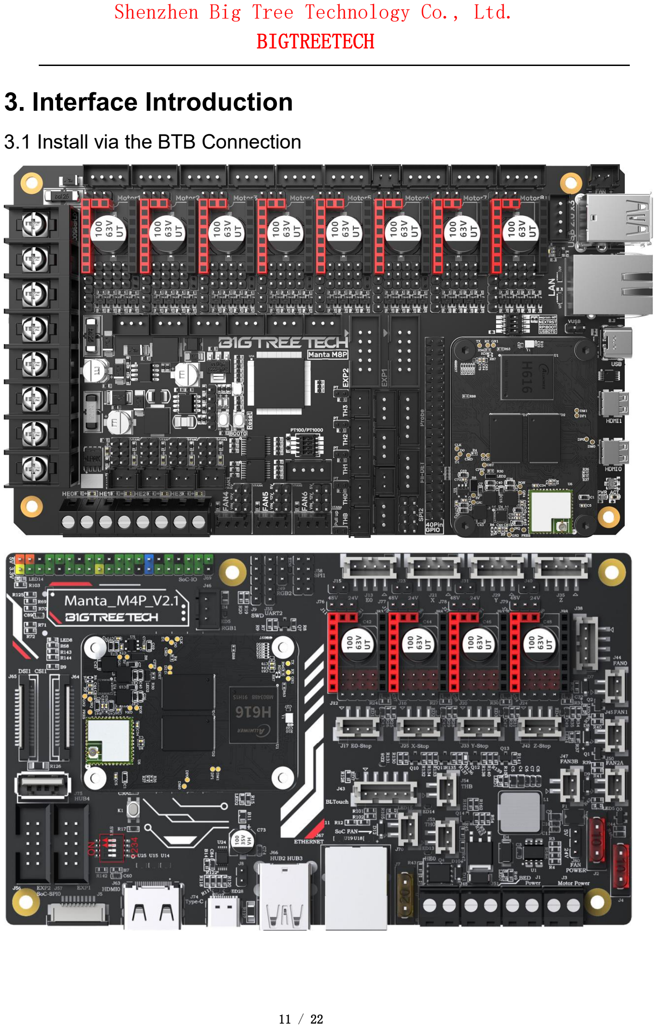
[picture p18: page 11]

11 / 22

## 3.1 Install via the BTB Connection

## BIGTREETECH

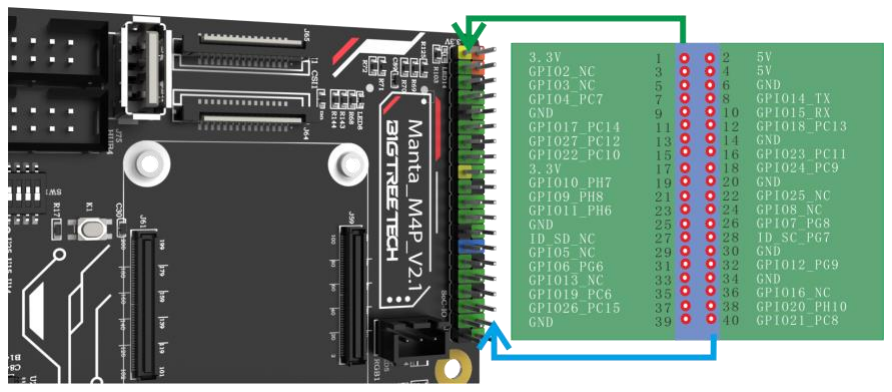
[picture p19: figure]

12 / 22

## 3.2 40 pins GPIO

When Manta series motherboard work with CB1, 40 pins GPIO is a custom IO arrangement, as shown in the figure below, Pin 7 is CB1's "PC7", and Pin 11 is CB1's "PC14". The GPIO number of CB1 corresponds to (Px–PA)*32 + Pin For example: PC7 = (PC–PA)*32 + 7 = 2 * 32 + 7 = 71 PH10 = (PH–PA)*32 + 10 = 7 * 32 + 10 = 234 PC7 is numbered in Klipper as pin: host: gpio71, PH10 as pin: host: gpio234

Note: The logic voltage of PC ports in V2.1 version (PC6, PC7, PC8, PC9, PC10, PC11, PC12, PC13, PC14, PC15): 1.8V;

The logic voltage of PC ports in V2.2 version (PC6, PC7, PC8, PC9, PC10, PC11, PC12, PC13, PC14, PC15): 3.3V.

## BIGTREETECH

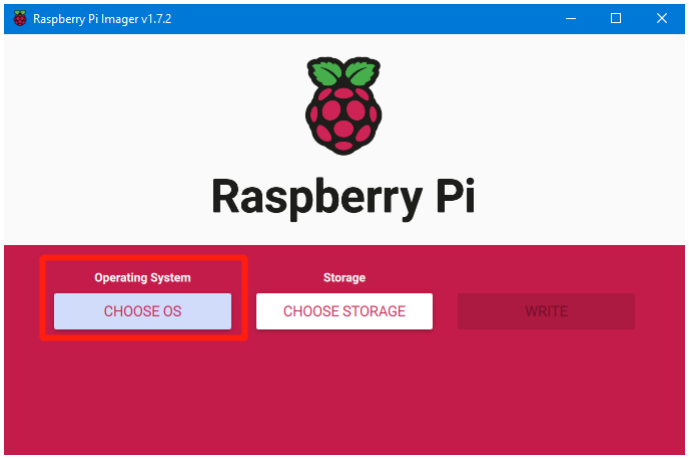
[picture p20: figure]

13 / 22

# 4. Write OS

## 4.1 Download the OS Image

### Please download and install the OS image we provided: https://github.com/bigtreetech/CB1/releases

## 4.2 Download and Install Writing Software

### The official Raspberry Pi Imager: https://www.raspberrypi.com/software/ balenaEtcher: https://www.balena.io/etcher/

Both of the above software can be used, just choose one to download and install.

## 4.3 Write OS

### 4.3.1 For Raspberry Pi Imager

a. Insert a MicroSD into your computer.
b. Choose OS.

## BIGTREETECH

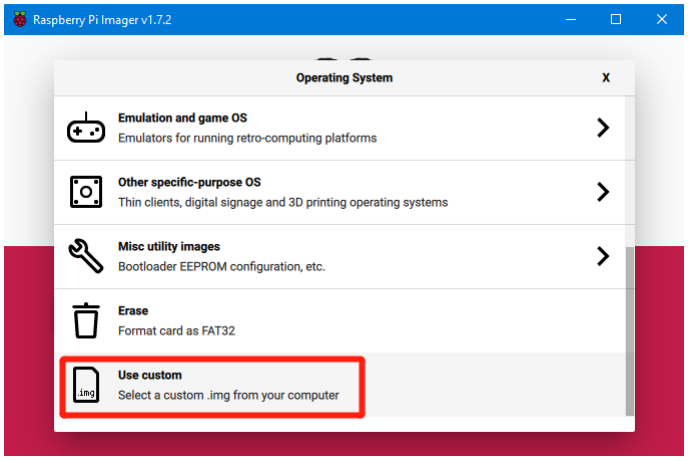
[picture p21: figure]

14 / 22

c. Select "Use custom", then select the image that you downloaded.

### d. Select the MicroSD card and click "WRITE" (WRITE the image will format the MicroSD card. Be careful not to select the wrong storage device, otherwise the data will be formatted.)

## BIGTREETECH

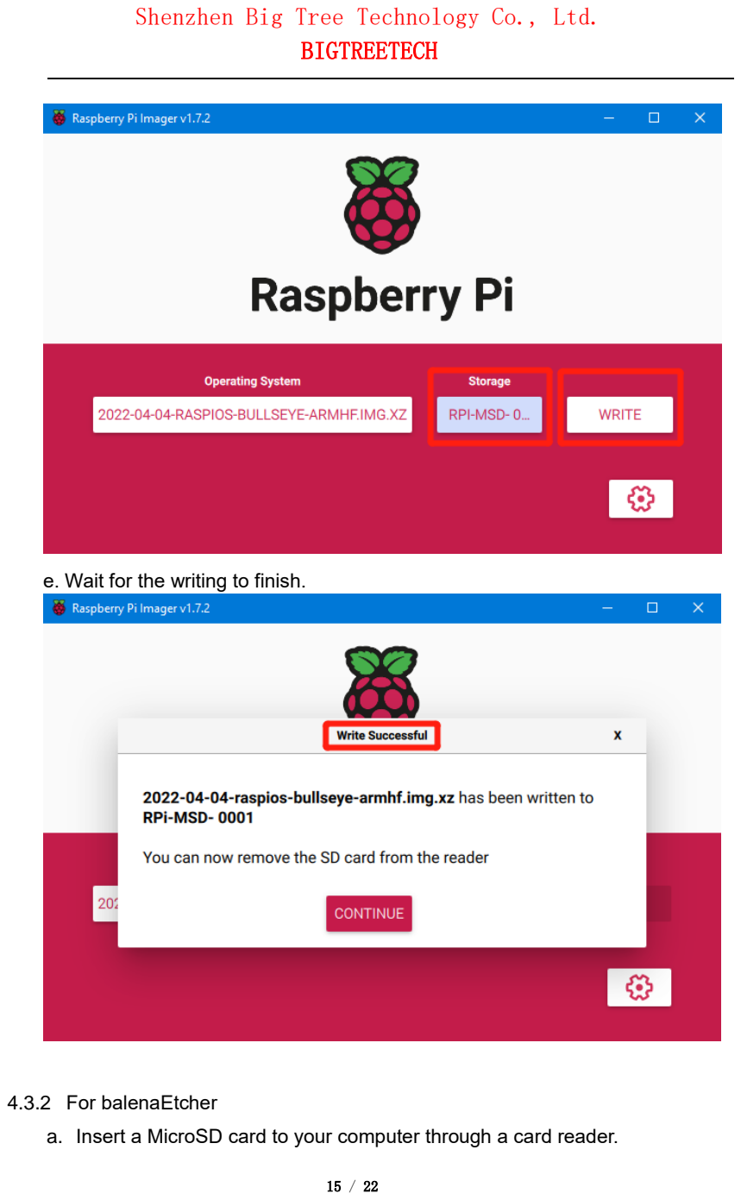
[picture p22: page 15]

15 / 22

e. Wait for the writing to finish.

### 4.3.2 For balenaEtcher

a. Insert a MicroSD card to your computer through a card reader.

## BIGTREETECH

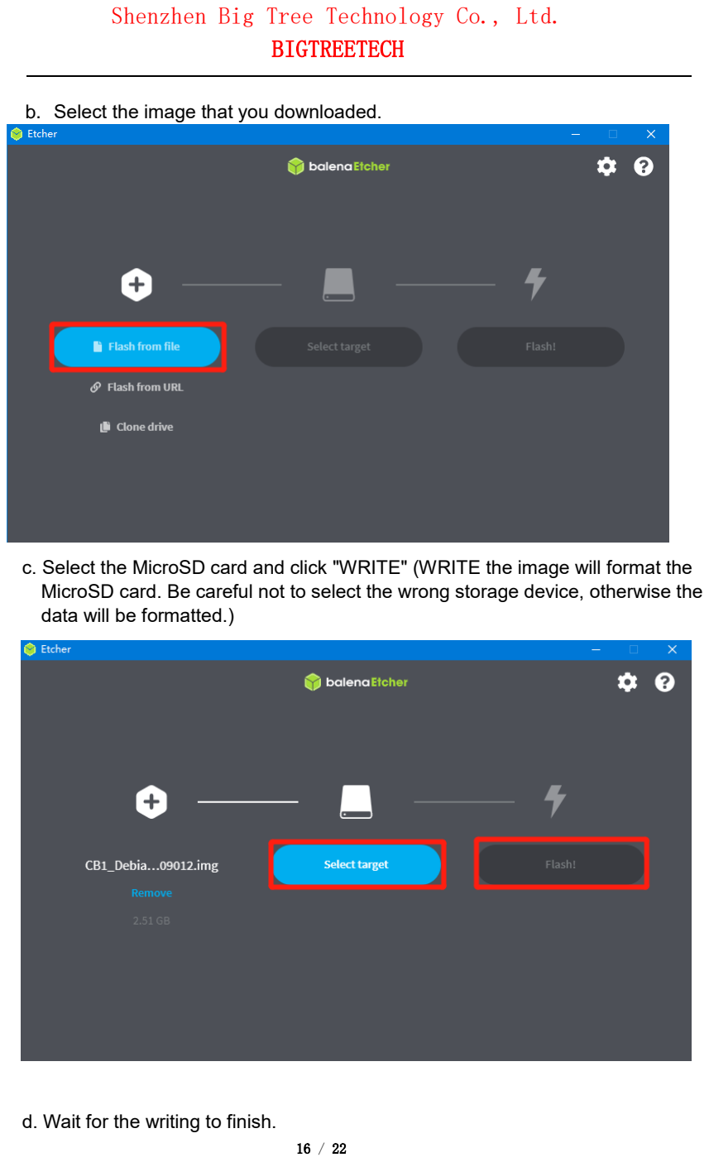
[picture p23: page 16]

16 / 22

b. Select the image that you downloaded.

### c. Select the MicroSD card and click "WRITE" (WRITE the image will format the MicroSD card. Be careful not to select the wrong storage device, otherwise the data will be formatted.)

d. Wait for the writing to finish.

## BIGTREETECH

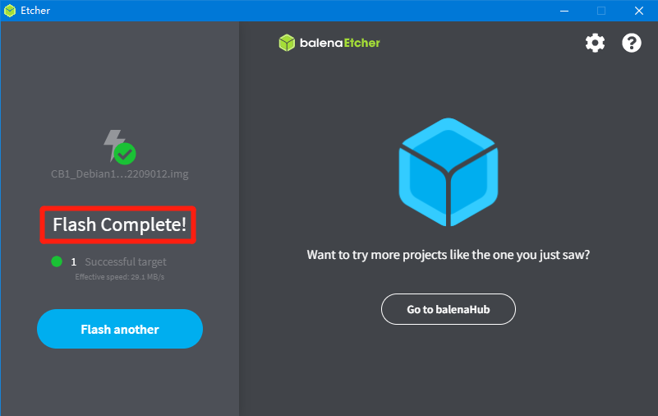
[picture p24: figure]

17 / 22

## BIGTREETECH

# 5. Configure Network

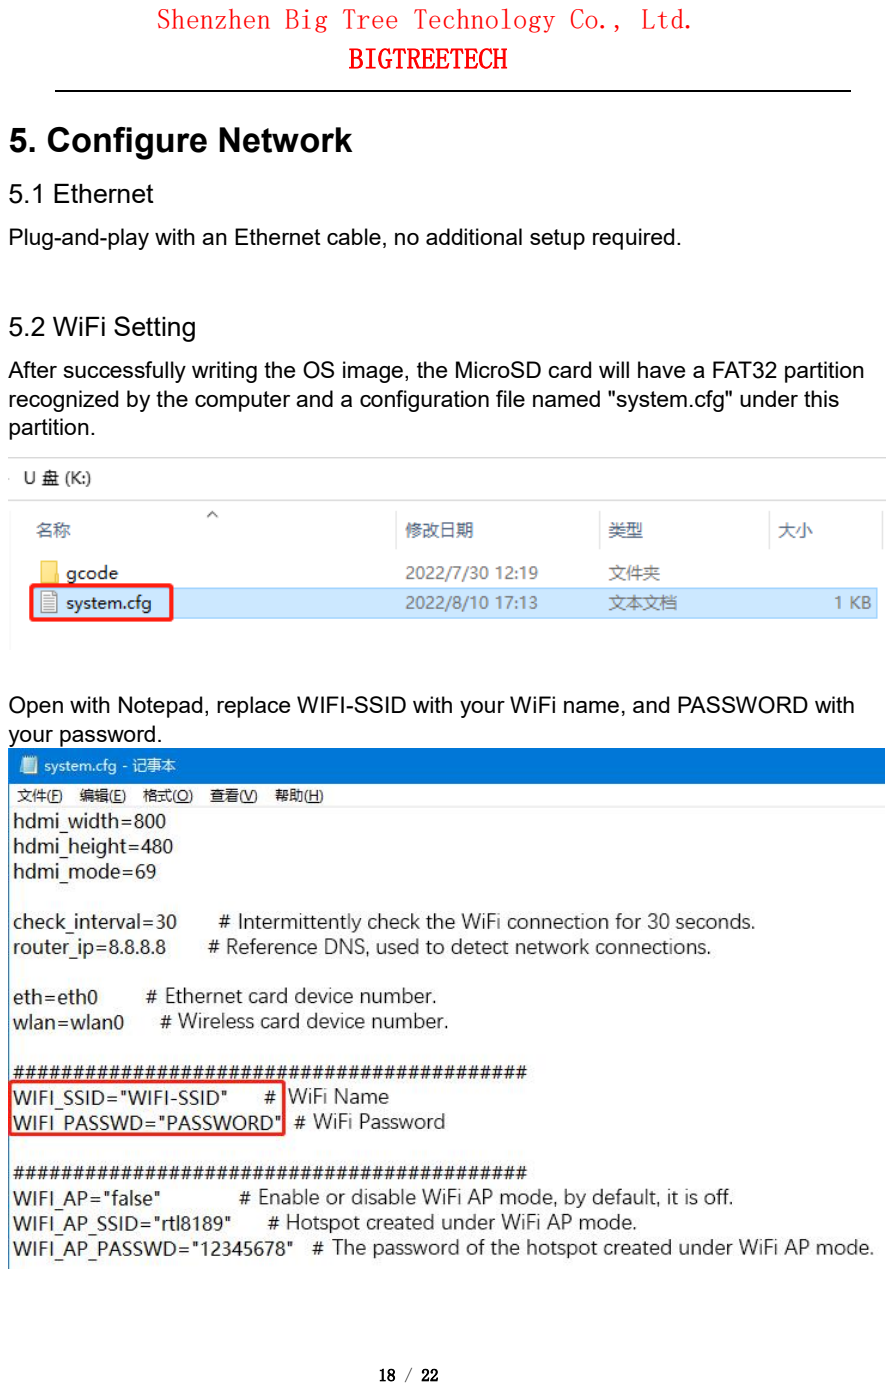
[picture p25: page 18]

18 / 22

## 5.1 Ethernet

Plug-and-play with an Ethernet cable, no additional setup required.

## 5.2 WiFi Setting

### After successfully writing the OS image, the MicroSD card will have a FAT32 partition recognized by the computer and a configuration file named "system.cfg" under this

partition.

### Open with Notepad, replace WIFI-SSID with your WiFi name, and PASSWORD with

your password.

## BIGTREETECH

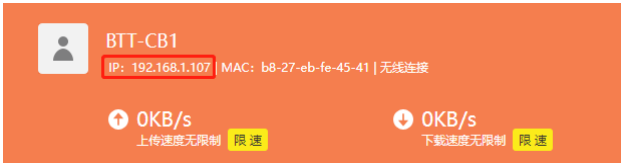
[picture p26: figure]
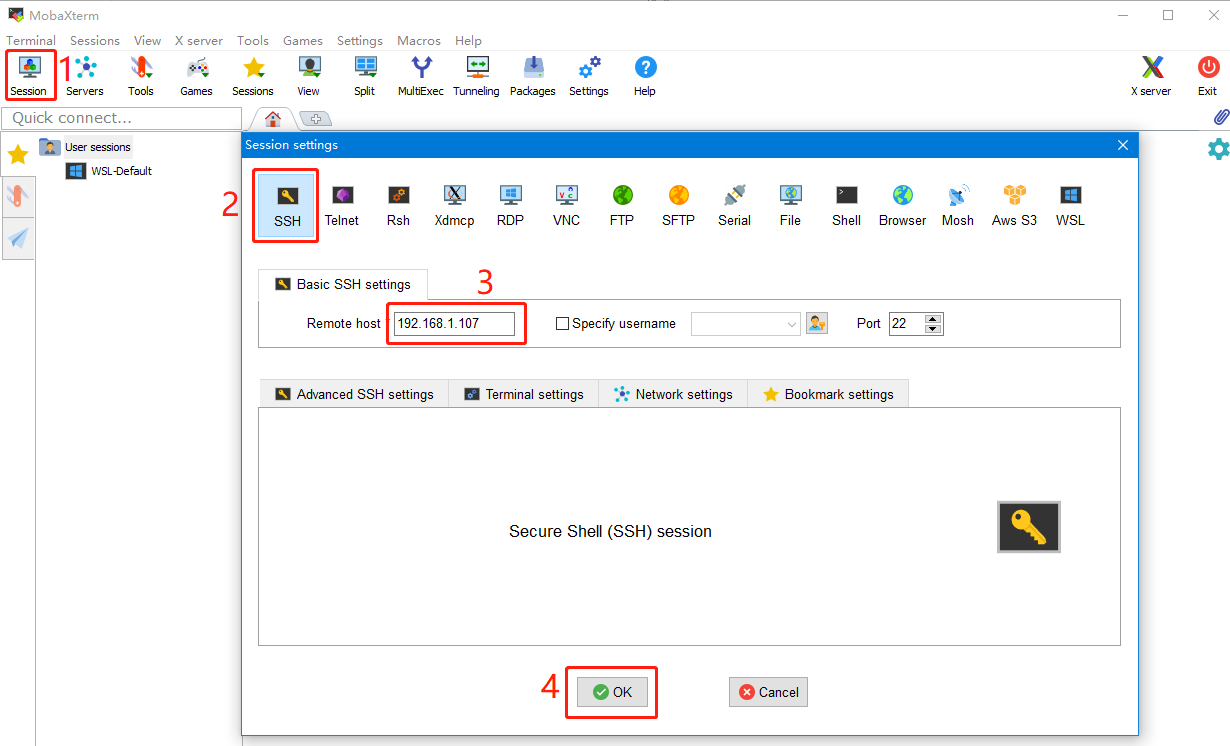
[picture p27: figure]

19 / 22

# 6. Configure Motherboard

## 6.1 SSH Connect to Device with CB1 Installed

### 1. Install the SSH application Mobaxterm: https://mobaxterm.mobatek.net/download-home-edition.html (https://mobaxterm.mobatek.net/download-home-edition.html)

### 2. Insert the MicroSD card to the motherboard, and wait for the system to load after

power on, approx. 1-2 minutes.

### 3. The device with CB1 installed will automatically be assigned an IP after being

successfully connected to the network.

4. Find the IP address on your router page.

### 5. Open Mobaxterm and click "Session", and click "SSH", enter the IP you got in step 3 into Remote host, and click "OK". (Note: your computer and the printer needs to be in the same network.)

## BIGTREETECH

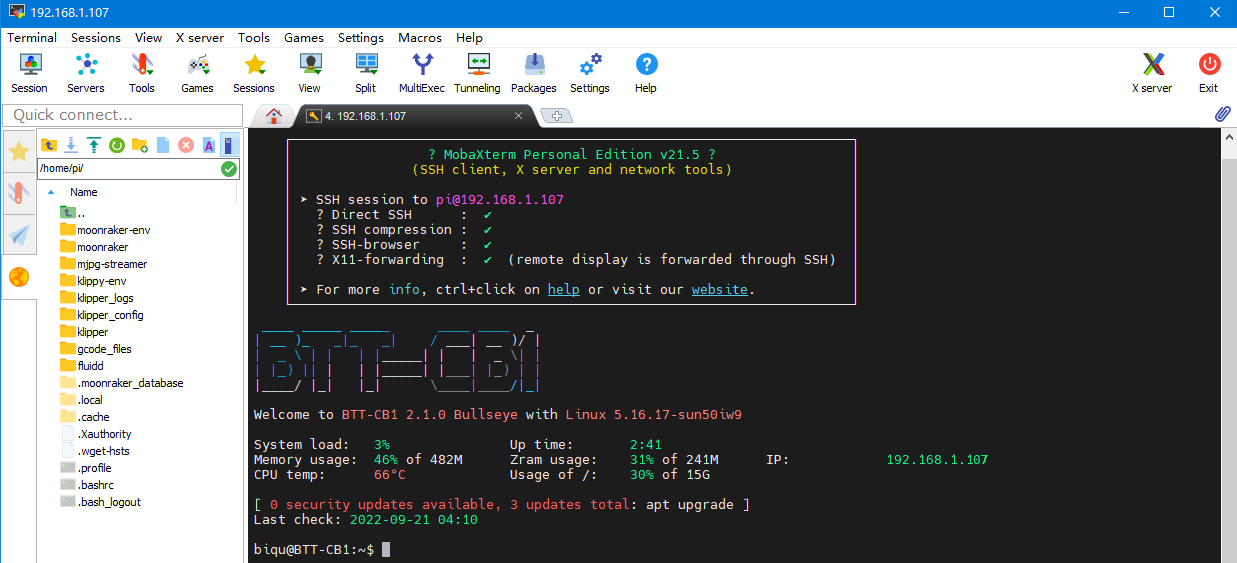
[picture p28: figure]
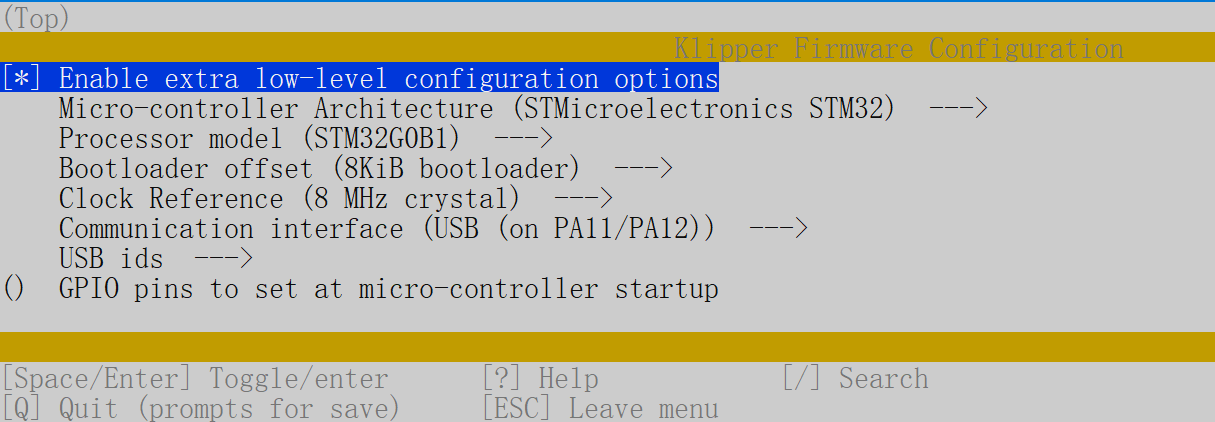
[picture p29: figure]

20 / 22

6. Login as: biqu, password: biqu.

## 6.2 Compile MCU Firmware

1. After SSH is successfully connected to the device with CB1 installed, enter in the terminal: cd ~/klipper/ make menuconfig Compile the firmware with the corresponding motherboard configuration, here is the Manta M4P example: * [*] Enable extra low-level configuration options * Micro-controller Architecture (STMicroelectronics STM32) ---> * Processor model (STM32G0B1) ---> * Bootloader offset (8KiB bootloader) ---> * Clock Reference (8 MHz crystal) ---> * Communication interface (USB (on PA11/PA12)) --->

## BIGTREETECH

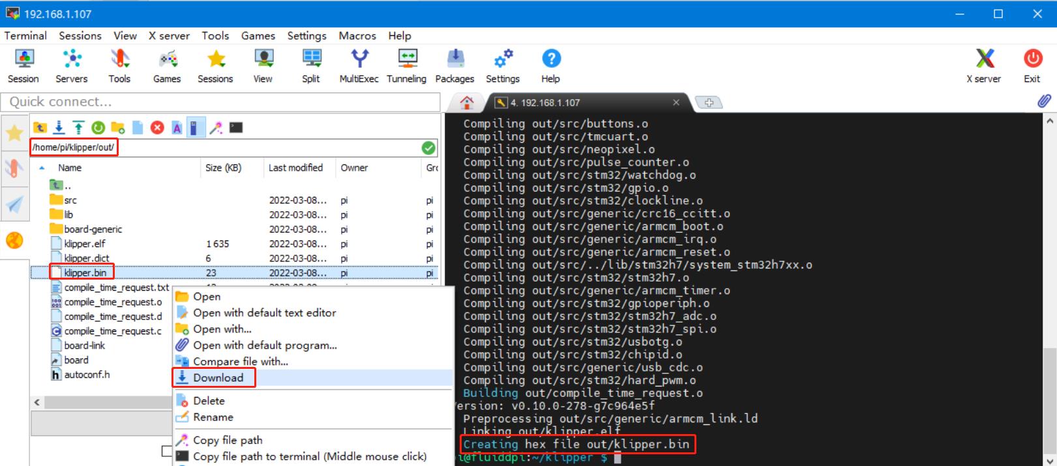
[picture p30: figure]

21 / 22

2. Press q to exit, and Yes when asked to save the configuration.
3. Run | make | to compile firmware, "klipper.bin" file will be generated in
home/pi/klipper/out folder when | make | is finished, download it onto your
computer using the SSH application.

## BIGTREETECH

22 / 22

# 7. Cautions

### - All unplugging and plugging operations should be performed under the condition of

power off, except for HDMI, USB, and RJ45.

### - Pay attention to the heat dissipation of CB1. If the running application consumes

too many system resources, the CB1 will get hot quite seriously.

If you need other resources for this product, please visit https://github.com/bigtreetech/

### and find them yourself. If you cannot find the resources you need, you can contact our

after-sales support.

### If you encounter other problems during use, feel free to contact us, and we are answering them carefully; any good opinions or suggestions on our products are welcome, too and we will consider them carefully. Thank you for choosing BIGTREETECH. Your support means a lot to us!

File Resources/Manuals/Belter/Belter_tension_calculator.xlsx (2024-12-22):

Display Reading (mm) | Belt Tension GT2 RF (N) | Tension Calculator |  |  | Printer Type and Model
5 | 4.65 | Belter Display Value(mm): Enter the Belter Display value in the blue area | 6.9 |  | Select your Printer and Belt type in green area |  | VZ330/250
5.1 | 5.42
5.2 | 6.19
5.3 | 6.95
5.4 | 7.72 | Belt Tension (N) | 19.23138075 |  | Recommended Tension |  | Is your tension within Range
5.5 | 8.49 |  |  |  | Min | Max | YES
5.6 | 9.26 |  |  |  | 12 | 20
5.7 | 10.02
5.8 | 10.79
5.9 | 11.56
6 | 12.33
6.1 | 13.09
6.2 | 13.86
6.3 | 14.63
6.4 | 15.39
6.5 | 16.16
6.6 | 16.93
6.7 | 17.70
6.8 | 18.46
6.9 | 19.23
7 | 20.00
7.1 | 20.77
7.2 | 21.53
7.3 | 22.30
7.4 | 23.07
7.5 | 23.84
7.6 | 24.60
7.7 | 25.37
7.8 | 26.14
7.9 | 26.91
8 | 27.67
8.1 | 28.44
8.2 | 29.21
8.3 | 29.97
8.4 | 30.74
8.5 | 31.51
8.6 | 32.28
8.7 | 33.04
8.8 | 33.81
8.9 | 34.58
9 | 35.35
9.1 | 36.11
9.2 | 36.88
9.3 | 37.65
9.4 | 38.42
9.5 | 39.18
9.6 | 39.95
9.7 | 40.72 | Machine LUT | Min | Max
9.8 | 41.48 | All Voron A/B Belts | 7.8 | 15
9.9 | 42.25 | Voron 2.4 Z belts | 20.4 | 25.8
10 | 43.02 | VZ330/250 | 12 | 20
10.1 | 43.79 | Custom Printer
10.2 | 44.55
10.3 | 45.32
10.4 | 46.09
10.5 | 46.86
10.6 | 47.62
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

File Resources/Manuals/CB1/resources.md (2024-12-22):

---
created: 2024-12-20T08:23
updated: 2024-12-20T08:23
---
Link : file:///media/random-canuck/VM%20USB/voron/Voron%20Manual/Hardware%20Config/CBT%20Kit%20Manta%20M8P%20V1%20+%20CB1%20Start%20Guide%20%E2%80%93%20MPX%20Wiki.html

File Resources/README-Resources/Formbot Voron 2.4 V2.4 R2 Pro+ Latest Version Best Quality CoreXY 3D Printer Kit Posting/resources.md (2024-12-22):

---
created: 2024-12-20T08:23
updated: 2024-12-20T08:23
---
Link: https://www.aliexpress.com/item/1005003385349518.html?spm=a2g0o.order_list.order_list_main.59.318318027IHoca
Documents: https://github.com/FORMBOT/Voron-2.4
Review and Guide: https://www.youtube.com/watch?v=7x-eafpESLc

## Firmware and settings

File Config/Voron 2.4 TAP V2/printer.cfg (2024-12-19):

##--------------------------------------------------------------------
# This file contains common pin mappings for the BIGTREETECH Manta M8P
# To use this config, the firmware should be compiled for the
# STM32G0B1 with a "8KiB bootloader" "8 MHz crystal"
# and "USB (on PA11/PA12)" or "CAN bus (on PD12/PD13)".

# See docs/Config_Reference.md for a description of parameters.
# See include generic-bigtreetech-manta-m8p-V1_1.cfg
##--------------------------------------------------------------------
######################################################################
###########     Voron 2.4 R2 Pro+ Formbot Kit May-2024     ###########
######################################################################
##--------------------------------------------------------------------
##---------------          SOFTWARE LIBRARIES          ---------------
##--------------------------------------------------------------------
[include mainsail.cfg]
[include fluidd.cfg]
[include led-control.cfg]
[include print_start-macro.cfg]

[virtual_sdcard]
path: /home/biqu/printer_data/gcodes
on_error_gcode: CANCEL_PRINT
path: ~/printer_data/gcodes
[display_status]
[pause_resume]

##--------------------------------------------------------------------
##---------------          HARDWARE LIBRARIES          ---------------
##--------------------------------------------------------------------
[include EBBCan.cfg]
[include steppers.cfg]


##--------------------------------------------------------------------
##-----------------          PRINTER CONFIG          -----------------
##--------------------------------------------------------------------
# host MCU service is preinstalled and ready to use with:
[mcu]
##	[X in MOTOR1] - B Motor
##	[Y in MOTOR2] - A Motor
##	[Z in MOTOR3 - MOTOR6] - Z0 - Z3 Motor
##	[E in MOTOR7] - Extruder
##	Obtain definition by "ls -l /dev/serial/by-id/" then unplug to verify
##--------------------------------------------------------------------
canbus_uuid: 702c161f28a9
#restart_method: command
# serial: /dev/serial/by-id/usb-Klipper_stm32g0b1xx_46002E000B504B4633373520-if00
# serial: /tmp/klipper_host_mcu
##--------------------------------------------------------------------

[printer]
kinematics: corexy
max_velocity: 350  
max_accel: 3000    			#Max 4000
max_z_velocity: 15 			#Max 15 for 12V TMC Drivers, can increase for 24V
max_z_accel: 350
square_corner_velocity: 5.0

[temperature_sensor MCU]
sensor_type: temperature_mcu

[temperature_sensor SoC]
sensor_type: temperature_host

[force_move]
enable_force_move: true

[safe_z_home]
home_xy_position: 152, 146
speed: 50
z_hop: 5 
z_hop_speed: 15
move_to_previous: false

#[homing_override]
#gcode:
    #G28 X Y
    #G0 G90 X152 Y146 
    #G28 Z 
    #G0 G90 Z5 
#axes: z

[quad_gantry_level]
##	Use QUAD_GANTRY_LEVEL to level a gantry.
##	Min & Max gantry corners - measure from nozzle at MIN (0,0) and 
##	MAX (250, 250), (300,300), or (350,350) depending on your printer size
##	to respective belt positions

#--------------------------------------------------------------------
##	Gantry Corners for 250mm Build
##	Uncomment for 250mm build
#gantry_corners:
#	-60,-10
#	310, 320
##	Probe points
#points:
#	50,25
#	50,175
#	200,175
#	200,25
	
##	Gantry Corners for 300mm Build
##	Uncomment for 300mm build
gantry_corners:
	-60,-10
	360,370
##	Probe points
points:
	20,23
	20,272
	280,272
	280,23

##	Gantry Corners for 350mm Build
##	Uncomment for 350mm build
#gantry_corners:
#	-60,-10
#	410,420
#	Probe points
#points:
#	50,25
#	50,275
#	300,275
#	300,25

#--------------------------------------------------------------------
speed: 200
horizontal_move_z: 5
retries: 5
retry_tolerance: 0.0075
max_adjust: 5



[exclude_object]

[bed_mesh]
speed: 50
#   The speed (in mm/s) of non-probing moves during the calibration.
#   The default is 50.
horizontal_move_z: 5
#   The height (in mm) that the head should be commanded to move to
#   just prior to starting a probe operation. The default is 5.
mesh_min: 20, 23
#   Defines the minimum X, Y coordinate of the mesh for rectangular
#   beds. This coordinate is relative to the probe's location. This
#   will be the first point probed, nearest to the origin. This
#   parameter must be provided for rectangular beds.
mesh_max: 280, 275
#   Defines the maximum X, Y coordinate of the mesh for rectangular
#   beds. Adheres to the same principle as mesh_min, however this will
#   be the furthest point probed from the bed's origin. This parameter
#   must be provided for rectangular beds.
probe_count: 6, 6
#   For rectangular beds, this is a comma separate pair of integer
#   values X, Y defining the number of points to probe along each
#   axis. A single value is also valid, in which case that value will
#   be applied to both axes. Default is 3, 3.
#split_delta_z: .025
#   The amount of Z difference (in mm) along a move that will trigger
#   a split. Default is .025.
#move_check_distance: 5.0
#   The distance (in mm) along a move to check for split_delta_z.
#   This is also the minimum length that a move can be split. Default
#   is 5.0.
mesh_pps: 4, 4
#   A comma separated pair of integers X, Y defining the number of
#   points per segment to interpolate in the mesh along each axis. A
#   "segment" can be defined as the space between each probed point.
#   The user may enter a single value which will be applied to both
#   axes. Default is 2, 2.
#algorithm: lagrange
#   The interpolation algorithm to use. May be either "lagrange" or
#   "bicubic". This option will not affect 3x3 grids, which are forced
#   to use lagrange sampling. Default is lagrange.
#bicubic_tension: .2
#   When using the bicubic algorithm the tension parameter above may
#   be applied to change the amount of slope interpolated. Larger
#   numbers will increase the amount of slope, which results in more
#   curvature in the mesh. Default is .2.
zero_reference_position: 152, 146
#   An optional X,Y coordinate that specifies the location on the bed
#   where Z = 0.  When this option is specified the mesh will be offset
#   so that zero Z adjustment occurs at this location.  The default is
#   no zero reference.
#faulty_region_1_min:
#faulty_region_1_max:
#   Optional points that define a faulty region.  See docs/Bed_Mesh.md
#   for details on faulty regions.  Up to 99 faulty regions may be added.
#   By default no faulty regions are set.
adaptive_margin: 5
#   An optional margin (in mm) to be added around the bed area used by
#   the defined print objects when generating an adaptive mesh.


[axis_twist_compensation]
#speed: 50
#   The speed (in mm/s) of non-probing moves during the calibration.
#   The default is 50.
#horizontal_move_z: 5
#   The height (in mm) that the head should be commanded to move to
#   just prior to starting a probe operation. The default is 5.
calibrate_start_x: 20
#   Defines the minimum X coordinate of the calibration
#   This should be the X coordinate that positions the nozzle at the starting
#   calibration position. This parameter must be provided.
calibrate_end_x: 280
#   Defines the maximum X coordinate of the calibration
#   This should be the X coordinate that positions the nozzle at the ending
#   calibration position. This parameter must be provided.
calibrate_y: 146
#   Defines the Y coordinate of the calibration
#   This should be the Y coordinate that positions the nozzle during the
#   calibration process. This parameter must be provided and is recommended to
#   be near the center of the bed



#####################################################################
# 	Bed Settings
#####################################################################

[heater_bed]
heater_pin: PB5
sensor_type: Generic 3950
sensor_pin: PA0 # TB
control: watermark
min_temp: 0
max_temp: 130

# Fan0
[controller_fan Stepper-Driver-Fan]
pin: PE6
stepper: stepper_x, stepper_y, stepper_z

#[fan_generic fan1]
#pin: PE0

#[fan_generic fan2]
#pin: PC12

#[fan_generic fan3]
#pin: PE5

# Fan4
[fan_generic Exhaust-Fan]
pin: PE4

#[heater_fan fan5]
#pin: PB8
#tachometer_pin: PC14

#[heater_fan fan6]
#pin: PB9
#tachometer_pin: PC15

#[heater_fan SoC_fan]
#pin: CB1:gpio79
#pin: RPI:gpio26

[board_pins]
aliases:
    # EXP1 header
    EXP1_1=PE9, EXP1_2=PE10,
    EXP1_3=PE11, EXP1_4=PE12,
    EXP1_5=PE13, EXP1_6=PE14,    # Slot in the socket on this side
    EXP1_7=PE15, EXP1_8=PB10,
    EXP1_9=<GND>, EXP1_10=<5V>,

    # EXP2 header
    EXP2_1=PB14, EXP2_2=PB13,
    EXP2_3=PF7, EXP2_4=PB12,
    EXP2_5=PE7, EXP2_6=PB11,      # Slot in the socket on this side
    EXP2_7=PE8, EXP2_8=<RST>,
    EXP2_9=<GND>, EXP2_10=<NC>

# See the sample-lcd.cfg file for definitions of common LCD displays.

#[bltouch]
#sensor_pin: PB2
#control_pin: PB1

# Proximity switch
#[probe]
#pin: PF6

#[output_pin ps_on_pin]
#pin: PC3

#[output_pin pc13_pin]
#pin: PC13

#[neopixel my_neopixel_1]
#pin: PA9

#[neopixel my_neopixel_2]
#pin: PB15

#[hall_filament_width_sensor]
#adc1: PC5
#adc2: PB0
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

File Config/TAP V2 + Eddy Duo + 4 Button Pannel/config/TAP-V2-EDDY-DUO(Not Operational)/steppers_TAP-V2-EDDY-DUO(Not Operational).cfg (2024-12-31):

#####################################################################
#   	X Stepper Settings
#####################################################################
##--------------------------------------------------------------------
## X Stepper on Motor1(B Motor)
# 300mm build
[stepper_x]
dir_pin: PB4
step_pin: PE2
enable_pin: !PC11
microsteps: 16
rotation_distance: 40
endstop_pin: EBBCan:gpio24
homing_speed: 20
homing_retract_dist: 5
## --------- Travel Limits ---------
position_endstop: 303
position_max: 303
#################
## TAP V2 ONLY ##
#################
# position_min = 0
# position_min = 3    # (+3mm Saftedy)

#######################
## TAP V2 + Eddy Duo ##
#######################
# position_min: 18.5
position_min = 21.5   # (+3mm Saftedy)

# Motor1
[tmc2209 stepper_x]
uart_pin: PC10
#diag_pin: PF3
run_current: 0.800
# ----------     DEFAULT (Always On)     ----------
# Stealchop_threashold: 999999 
# Should be quieter but when at 999999, causes loud girinding noise when moving diagonal
# Need to figure out why steathchop is not quieter thatn spreadcycle. Maybe interpoaltion: true or false?
stealthchop_threshold: 0

#####################################################################
#   	Y Stepper Settings
#####################################################################
## Y Stepper on Motor2 (A Motor)
# 300mm build
[stepper_y]
dir_pin: PF11
step_pin: PF12
enable_pin: !PB3
microsteps: 16
rotation_distance: 40
endstop_pin: ^PF4
position_min: 5
#homing_positive_dir: true
homing_speed: 20  #Max 100
homing_retract_dist: 5
## --------- Travel Limits ---------
position_endstop: 305
position_max: 305
position_min: 5

# Motor2
[tmc2209 stepper_y]
uart_pin: PF13
#diag_pin: PF4
run_current: 0.800
stealthchop_threshold: 0

#####################################################################
#   	Z Stepper Settings
#####################################################################
##	Z Stepper - Front Left on Motor3_A
[stepper_z]
dir_pin: PD6
step_pin: PD7
enable_pin: !PF10
microsteps: 16
rotation_distance: 32 ##16-tooth pully of stepper * 2mm belt picth
gear_ratio: 80:20
#endstop_pin: ^PF5
##  Z-position of nozzle (in mm) to z-endstop trigger point relative to print surface (Z0)
##  (+) value = endstop above Z0, (-) value = endstop below
##	Increasing position_endstop brings nozzle closer to the bed
##  After you run Z_ENDSTOP_CALIBRATE, position_endstop will be stored at the very end of your config
#position_endstop: -0.5
endstop_pin: probe:z_virtual_endstop
homing_speed: 10
second_homing_speed: 3
homing_retract_dist: 5
## --------- Travel Limits ---------
position_max: 290
position_min: -2

# Motor3
[tmc2209 stepper_z]
uart_pin: PF9
#diag_pin: PF5
run_current: 0.650
stealthchop_threshold: 0

#####################################################################
#   	Z1 Stepper Settings
#####################################################################
##	Z1 Stepper - Rear Left on Motor4
[stepper_z1]
dir_pin: !PD2
step_pin: PD3
enable_pin: !PD5
microsteps: 16
rotation_distance: 32 ##16-tooth pully of stepper * 2mm belt picth
gear_ratio: 80:20

# Motor5
[tmc2209 stepper_z1]
uart_pin: PD4
run_current: 0.650
stealthchop_threshold: 0

#####################################################################
#   	Z2 Stepper Settings
#####################################################################
##	Z2 Stepper - Rear Left on Motor5
[stepper_z2]
dir_pin: PC8
step_pin: PC9
enable_pin: !PD1
microsteps: 16
rotation_distance: 32 ##16-tooth pully of stepper * 2mm belt picth
gear_ratio: 80:20 

# Motor5
[tmc2209 stepper_z2]
uart_pin: PD0
run_current: 0.650
stealthchop_threshold: 0

#####################################################################
#   	Z3 Stepper Settings
#####################################################################
##	Z3 Stepper - Rear Left on Motor6
[stepper_z3]
dir_pin: !PA14
step_pin: PA10
enable_pin: !PA15
microsteps: 16
rotation_distance: 32 ##16-tooth pully of stepper * 2mm belt picth
gear_ratio: 80:20 

# Motor6
[tmc2209 stepper_z3]
uart_pin: PF8
run_current: 0.650
stealthchop_threshold: 0

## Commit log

2024-12-19 Add files via upload
    Current Working Build:
    Manta M8PV1.1
    CB1
    TMC2209
    EBB SB2209 CAN RP2040
    TAP V2
    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
    [EBBCan.cfg, fluidd.cfg, led-control.cfg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]
2024-12-22 added readme and some resources for walkthrough
    [BTT Eddy Clip v3.step, Belter_tension_calculator.xlsx, EBBCan.cfg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]
2024-12-22 removed duplicated first commit
    [EBBCan.cfg, fluidd.cfg, led-control.cfg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]
